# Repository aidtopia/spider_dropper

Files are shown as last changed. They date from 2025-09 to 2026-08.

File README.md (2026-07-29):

# Stupidly Simply Spider Dropper

by Adrian McCarthy

A mechanism to "drop" a spider (or other lightweight prop) for Halloween fun.

## Overview

There are several versions of spider droppers out there.  Most require a microcontroller (like an Arduino Uno) and two actuators (for example, a motor to spool up the spider and a servo or solenoid to initiate the drop).  There are single-motor versions, but they require a reversing motor (which doesn't "drop" the spider so much as lower it) and a motor controller.

There's also at least one commercial "dropping spider" available at Halloween stores and party stores.  Those put the mechanism in the body of a comically unrealistic spider.

Although I enjoy programming and more complex projects, I wanted to make a spider dropper that required fewer parts (a.k.a. cheaper) and would be accessible to haunters who aren't interested in electronics, microcontrollers, and programming.

So I came up with the Stupidly Simple Spider Dropper.

("Stupidly Simple" refers to the design of the mechanism, not the haunters who use them.  The name is inspired by the KISS principle:  Keep It Simple, Stupid.)

There are three configurations:

1. Stupidly Simple Spider Dropper AC
2. Stupidly Simple Spider Dropper DC
3. Stupidly Simple Spider Dropper DC with the Slightly Smarter upgrade.

In the `docs` subfolder, you'll find the [Assembly Instructions](docs/assembly.md) as well as the [User Guide](docs/user_guide.md).

The `notes` subfolder is a hodgepodge of design ideas and information.

The `parts` subfolder has the OpenSCAD files that generate the 3D-printable parts (and some tools to help assemble them).  It also has a spreadsheet of what parts are needed, as well as links to specific items that I've used and some approximate pricing information.

The `schematics` subfolder has the KiCad files for the Slightly Smarter circuit.

## History

I'm a member of the Northern California Haunters Group.  We meet up several times a year to build Halloween props.  During a brainstorming session for the following year's Make & Take calendar, a fellow haunter suggested spider droppers.

There are several such projects online, but I think her suggestion may have been inspired specifically by [Arduino Dropping Spider Halloween Widget 62](https://www.youtube.com/watch?v=s5qQ0CaRchc) on the NYC CNC YouTube channel.  It's a neat project that has a mechanism using two servo motors (requiring modifications to one of them), an Arduino, and a ultrasonic distance sensor.  The immediate reaction from others in the group was that it was too ambitious to make in a few hours on a Saturday.  And that was probably true.

But it got me wondering whether there might a simpler way to achieve the same effect.  What if I could devise a 3D-printable mechanism that required only one motor to drive the drop and the reset?  Could it be done without a microcontroller?  Would a continuous drop-and-reset cycle provide creepy ambiance?

I had some "reindeer" motors left over from a previous project.  These are synchronous motors geared down to 6 RPM in a weather-resistant housing.  They're very light duty, but a toy spider isn't very heavy.  If I could base the cycle around one revolution of the motor, that would repeat every 10 seconds, which felt like a good pace.  My hope was that the dropper would be simple and inexpensive enough that a haunter could deploy a few of them in a spider-infested haunt to create creepy ambient motion.

The trick was to figure out how to have two different phases:  dropping and winding.  After trying to think up cam-driven mechanisms, I came up with the key idea that's powered this project:  A drive gear with a toothless section that allows the spool to spin freely.

I 3D-printed multiple prototypes trying to implement the idea.  The basic idea worked, but the spider bounced and spun around too much.  And the mechanism was prone to jamming when the bounce created enough slack to cause the string to get tangled in the mechanism.

I thought the solution was going to be to use elastic string to dampen the bounce from the sudden stop at the bottom of the drop.  I gave out a couple prototypes to fellow haunters to beta test in their displays.  The elastic string had made things worse.  The bounces were even more chaotic, and the spider's legs would get tangled in the string.  When it was hoisted back up, the spider would reach the top too soon and lock up the mechanism.  One of my beta testers painstakingly attached thread to the tips of each spider leg to keep the elastic string from getting between the legs.

On and off over the next couple years, I iterated on the design.  Elastic string was out.  Regular string (like kite string) was also problematic: The tension in the braid makes the spider want to spin like an ice skater, and, over time, it gets stretched out.  A big breakthrough was using monofilament (fishing line).  With a better spool design, monofilament is much less prone to tangling.

I switched to an open framework base plate because I thought it would look cool and be easier to experiment.  The unexpected benefit was that the open base plate doesn't amplify the motor noise.  The original slab design resonated with the motor vibrations, making it significantly louder.

I added skate bearings to the spool to reduce friction and avoid wear of the plastic parts.  This too had an unexpected (and more important) effect:  The additional rotational inertia of the bearings causes the spider to drop more smoothly, which looked better and further reduced problematic bouncing.

At some point, another Norcal haunter mentioned that he would be more interested in a DC version than one that uses an AC reindeer motor.  I searched around and found the JGY-370 motors, which are available with gear reduction to 6 RPM, just like the reindeer motors.  I made the base plate accommodate both styles of motor mount, but that still required two versions of the gears and spools due to differences in the shaft height and diameter.  I factored out those differences by creating the shaft adapaters which allow the rest of the mechanism to be motor-agnostic.

Despite all the progress, I grew bored with the project.  The continuous operation just wasn't as interesting as a drop triggered by the presence of the victim.

Around this time, I was playing around with mini PIR motion sensors.  PIR motion sensors generally aren't the right solution for triggering a startle effect because they're sensitive over a large area.  Haunters often try to control the field of view by recessing the sensors in a bit of PVC pipe, which helps but can be bulky.  And older sensors generally require a microcontroller to deal with "settling time" and "debouncing."  But these newer PIR sensors have a built-in microcontroller that handles those details.  These were small enough to fit into a discreet 3D-printed housing to control the detection zone.  In fact, I'd already designed such a housing.  I had even figured out how to reduce false triggers from distant motion.  They could be powered with 12 volts, the same voltage as the DC motors.  And they were inexpensive.

With what I'd learned about these newer PIR motion sensors, I realized I could start the DC motor turning with a simple circuit.  The only trick would be to turn the motor off just before the spider was about to drop.  I was vaguely aware of the "park" feature in windshield wiper motors, so I studied how those worked.  That was the last puzzle piece in the design of the Slightly Smarter upgrade.

And that inspired me to further refine the design until I had a kit design I felt good enough to share with other.

## Thanks To

Lynn for proposing a spider dropper Make & Take all those years ago.

CNC NYC for their inspiring spider dropper project.

Rex for teaching me enough about electronics to be dangerous, for opening my eyes to 3D printing and OpenSCAD, and for coming along on the journey from learning KiCad to making a custom PCB.

Ralph, Gigi, Mike, and Phyllis for beta testing and feedback.  Ralph and Gigi also helped me keep my mind open to mechanical solutions.  Mike for inspiring deeper exploration of sensors for triggering props.

DJ and Ernie who stress tested the first Slightly Smarter Spider Dropper in a real-life haunt during Halloween.

Mendora, Britta, and Glen for showing me that there is enough demand for the Stupidly Simple Spider Dropper to keep me motivated.

Jeff for helping out our fellow haunters with their soldering skills.

Suzanne for always reminding me that the techie projects need the crafty bits, too.

Kristi and Scott for hosting the (first?) Norcal Haunters Spider Dropper Make & Take.

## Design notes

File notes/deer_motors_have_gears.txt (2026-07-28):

Conversation with ChatGPT
2026-07-26
------

Today 7:25 AM
I've been building animated Halloween props with what are commonly called "reindeer" motors.  Suppliers like Fright Props and Monster Guts sell these as "small prop motors."  They plug into a regular 120 V outlet and run at approximately 6 RPM.  I opened the weather resistant housing on one that was no longer working well.  Inside there's what looks to be a common synchronous motor, similar to https://en.wikipedia.org/wiki/Synchronous_motor#/media/File:Synchronmot.jpg, but that's not the same model.  What I'm wondering is whether that motor uses gears.  The one that isn't working well had been connected to a mechanism that jammed.  Since clearing the jam, the motor frequently slips, making a ticking sound.  I think a gear was damaged when it had been jammed, but I've been told that synchronous motors like these do not have internal gears.  I tried to open the motor to do a post-mortem examination, but the metal case is crimped beyond my ability to pry it apart.  I noticed that the top plate has five little holes through which protrude the tips of pins (just like the one in the picture).  I suspect those may be axles for a gear train.  My theory is that, while the mechanism was seized up, one or more gear teeth were damaged, and now those broken teeth are prone to slip, causing the ticking sound.  (To be clear, my goal is not to repair this motor--it's history.  I'm just trying to learn about the failure mode in order to improve my future designs.)

Your theory is quite plausible, and the answer depends on which part of the assembly you're calling the motor.

The actual AC synchronous motor inside these "reindeer motors" almost certainly does not contain reduction gears. The motor itself is usually just:

A stator energized directly from 120 V AC.

A permanent magnet (or hysteresis-type) rotor that locks to the AC line frequency.

Bearings or bushings.

That motor spins much too fast to directly produce 6 RPM. On 60 Hz power, a common synchronous motor might run at 1800 RPM, 3600 RPM, or another speed depending on its pole count. Something has to reduce that speed by hundreds of times.

The reduction is almost always accomplished by a gear train attached to the motor, typically enclosed in the same crimped metal can. Manufacturers often sell the whole assembly as a "synchronous motor," even though it's really a synchronous motor plus gearbox.

The five little pins you noticed are a strong clue. They are very likely the ends of shafts supporting the intermediate gears.

A typical construction looks something like this:

Rotor
  │
Small pinion
  │
[Gear 1]
  │
[Gear 2]
  │
[Gear 3]
  │
...
  │
Output shaft (6 RPM)
Those little gear shafts often protrude through the stamped metal plate exactly as you described.

Why the ticking?
Several failure modes are possible after a jam.

1. Stripped or chipped gear teeth (your hypothesis)

This is probably the most common.

A reduction gearbox for a 6 RPM output has an enormous gear reduction, and the last few gears transmit the highest torque. If the output shaft is prevented from turning, those gears see the greatest stress.

If one tooth breaks off:

the gears mesh normally,

the damaged tooth arrives,

the gear slips or jumps,

you hear a click or tick,

then everything continues until the damaged tooth comes around again.

If the output rotates at 6 RPM, a damaged tooth on one of the final gears would produce a regular tick every revolution or several ticks per revolution, depending on which gear is damaged.

2. A cracked gear hub
Many inexpensive gearboxes use molded nylon gears press-fit onto steel shafts.

Instead of losing teeth, the hub can split.

Under load:

the gear rotates until torque builds,

the hub slips on the shaft,

it snaps back into engagement,

producing a ticking sound.

This is another very common failure after a stall.

3. Bent shaft or displaced bearing
Less common, but if a gear shaft shifts slightly, the gears don't mesh correctly and can ratchet over one another.

4. Rotor slipping?
People sometimes describe these motors as "slipping," but a true synchronous rotor doesn't normally ratchet under normal operation.

If overloaded enough, a synchronous motor can simply lose synchronism and stop producing useful torque. That doesn't usually create a regular mechanical tick. The fact that you're hearing distinct mechanical clicking strongly points toward the gearbox rather than the electromagnetic portion of the motor.

Why didn't the motor simply burn out?
A good question.

These motors produce very little power—often only a few watts. During a stall, several things can happen before the windings overheat:

plastic gears fail,

gear hubs crack,

teeth shear,

output shafts twist,

couplings fail.

Manufacturers often prefer the gearbox to be the sacrificial component because replacing a few molded gears is cheaper than rewinding a motor (even though, in sealed units like yours, neither is really intended to be serviced).

Can the gears really survive that much reduction?
Yes. A 6 RPM output from a synchronous motor requires an overall reduction on the order of hundreds to one.

For example:

1800 RPM motor → 6 RPM output

Reduction ratio ≈ 300:1

That generally takes several gear stages. It's entirely normal to find anywhere from 5 to 10 gears inside one of these little gearmotors.

The five pins
The five protruding pins are almost certainly not electrical.

They're typically:

gear shaft supports,

riveted or press-fit shaft ends,

or bearing pins for the intermediate gears.

That matches the construction used in many inexpensive synchronous gearmotors.

Does this fit your experience?
Very well.

You described:

mechanism jammed,

jam later cleared,

motor now ticks,

output intermittently slips.

That sequence is almost a textbook description of a damaged reduction gearbox. If I had to rank the likely causes, I'd put them in this order:

Chipped or stripped nylon gear tooth (most likely).

Cracked plastic gear hub.

Shifted gear shaft or bearing.

Damage to the synchronous motor itself (least likely).

Given that these "reindeer motors" are designed for very light-duty animated props, it's worth treating them as though they have essentially no stall tolerance. If there's any chance a linkage can jam, adding a compliant element (such as a spring, friction clutch, or flexible coupling) or ensuring the linkage reaches a mechanical stop before the motor is forced into a hard stall can significantly reduce the likelihood of gearbox damage. Your observations are consistent with the gearbox, not the synchronous motor proper, being the component that failed.

That's a really interesting failure mode, and it's exactly the kind of thing that's hard to appreciate until you've built a few iterations.

The fact that you're using flats on the shaft changes the picture considerably. The set screws aren't transmitting torque by friction; they're acting as keys against the flats. That means the required clamping force is much lower than it would be on a round shaft. The problem isn't that the screws lose friction—it's that the geometry changes just enough that they stop engaging the flats effectively.

It's astonishing how little movement is required for the set screws to become irrelevant.

I believe it. Mechanically, it's a tipping point. As long as the screw tip is bearing squarely on the flat, it positively resists rotation. Once the insert or nut tilts by even a fraction of a degree, the contact patch shifts, the screw starts riding up the corner radius or loses full engagement, and the effective torque capacity collapses. It doesn't take much.

The fact that you see different implementations (captured nuts vs. heat-set inserts) failing in essentially the same way suggests the culprit isn't the hardware—it's the PETG creeping under sustained compressive load.

PETG is great for many things, but it has a reputation for exactly this behavior. Under constant stress it will slowly "flow" at room temperature. That's one reason it's often described as being tougher than PLA but less dimensionally stable under load.

What's especially challenging in your application is that Halloween props are almost the perfect environment for creep:

The coupler is under nearly constant torque while lifting the spider.

Every cycle repeats the load.

October decorations may sit in the sun during the day, and PETG's stiffness drops noticeably as temperature rises.

The mechanism spends hours cycling, giving the polymer plenty of time to relax.

None of those loads is particularly high individually, but creep doesn't require high stress if you give it enough time.

One thing your experience makes me wonder is whether the coupler itself is actually trying to solve two conflicting problems:

Be rigid enough to maintain the alignment of the threaded inserts.

Be compliant enough to become the sacrificial element.

Those goals are almost opposites.

If I were experimenting, I probably wouldn't start by changing the overload protection at all. I'd first try to eliminate creep as the dominant wear mechanism.

For example, instead of the inserts being supported only by plastic, imagine a tiny steel "bridge" between the two opposing screws. Then the plastic would only locate that bridge rather than resisting the screw forces directly. Even a thin stamped plate or a short piece of steel tubing could dramatically reduce deformation.

Another thought is to avoid point loading entirely. A split-clamp style coupler—the kind used on shaft collars—loads the plastic much more uniformly than two opposing set screws. The screws stretch the clamp instead of pushing directly into the shaft. Whether that's printable in your available space is another matter, but mechanically it's a much friendlier way to use plastic.

I also keep coming back to your original observation that the gearbox failed before the coupler.

That may simply mean the gearbox's failure torque is surprisingly low. We tend to associate "gearbox" with something robust, but the gear train inside these synchronous motors is often made from tiny acetal or nylon gears only a few millimeters across. A tooth root might be less than a millimeter thick. Even if the motor can only deliver a few watts, the reduction ratio means the last gear can see enough torque to exceed the strength of those tiny teeth.

So I don't think your coupler was "wrong." It may have been appropriately calibrated for a metal-geared DC motor and simply too slow-acting for a gearbox that has much less overload margin.

One question out of curiosity: do you know whether the failed reindeer motor had all-plastic reduction gears, or did it have a mix of metal and plastic? Some of the inexpensive synchronous gearmotors use a steel first pinion with plastic intermediate gears, while others have one or two sintered-metal gears near the output. If you could identify the gear materials, it would tell us a lot about where the designer expected the weakest link to be.

"A split-clamp style coupler": That's not practical to retrofit into the current design, but it's definitely on my list for future projects.  "do you know whether the failed reindeer motor had all-plastic reduction gears":  No I don't know; that's what I was hoping to find out by opening it, which I was unable to do.  "instead of the inserts being supported only by plastic, imagine a tiny steel "bridge" between the two opposing screws.":  I'm having trouble picturing what you're describing in that paragraph.  Keep in mind that some motors have a single flat side and others have two opposing flat sides.  Even in the latter case, a "bridge" between the opposing set screws would have to pass through the motor shaft.  So I must not understand what you're proposing here.

You're right—that idea doesn't survive contact with the actual geometry. I was mentally picturing a larger shaft with enough room to have the screws bear against a separate steel element, but with a 5–6 mm motor shaft occupying the middle, there's literally nowhere for a bridge between opposing screws to go. So you can disregard that suggestion.

Given what you've described, I actually think you've done a pretty thoughtful job with the coupler. You're dealing with a difficult combination of constraints:

Small shaft diameter.

Limited radial space.

Plastic construction.

Need for intentional overload protection.

Need for long-term dimensional stability.

Those goals all pull in different directions.

One thing that occurred to me, though, is that you're relying on set screws in compression. Plastic is generally weakest in that mode because it creeps under concentrated bearing loads.

If you were designing from scratch, I'd be inclined toward a split-clamp not because it holds more torque, but because the screws would be putting the plastic primarily into tension. Plastics generally tolerate that much better over time. But as you say, that's a future-project idea, not something to retrofit.

Your description of the failures also made me think of something else.

You said:

Most early designs worked perfectly for dozens of cycles, but started slipping more and more.

That's almost the textbook signature of creep, not wear.

If the inserts were wearing loose, I'd expect a more abrupt change once enough material was lost.

If they're creeping, the holding torque should decrease gradually over time—which is exactly what you observed.

As for the gearbox, one way you might satisfy your curiosity without opening this particular motor is to sacrifice a new one.

That sounds counterintuitive, but hear me out.

If these are inexpensive commodity synchronous gearmotors housed in a custom weatherproof enclosure, there's a decent chance that every unit from that supplier uses the same gear train. Opening a new one with a cutoff wheel would let you document:

number of reduction stages,

gear materials,

shaft diameters,

whether the last gears are plastic or metal,

how the shafts are supported.

Then you could compare that construction with the symptoms from your failed motor and probably infer what broke.

One thing I find particularly elegant about your spider mechanism is the toothless-sector release. It's one of those ideas that's obvious only after someone tells you. Using the drive gear itself as the timing element eliminates the need for a clutch, solenoid, or cam. That's the kind of mechanical simplification I enjoy seeing.

It also makes me wonder whether there's another place to introduce overload protection.

Instead of protecting the motor, perhaps protect the spool.

Suppose the spool had a tiny compliant hub—not enough to slip continuously, just enough to twist a few degrees under overload. During normal lifting, you'd never notice it. During a jam, it would absorb the initial shock before the gearbox saw the full torque.

I'm not thinking of a friction clutch this time. More like a torsion spring built into the spool itself, or a hub with thin flexible webs. Because it's only storing a few degrees of twist, it could potentially fit in almost the same envelope as your existing spool.

It wouldn't replace your existing coupler—it would complement it. The compliant spool would absorb the first few milliseconds of the overload (where gear teeth are most vulnerable), and if the jam persisted, your coupler would eventually slip as it already does.

Whether that's worth the added complexity is another question. But it's the kind of solution that addresses the distinction between shock protection and stall protection that we've uncovered in this discussion.

I have to say, this has been an enjoyable engineering conversation. You're clearly doing what good machine designers do: not just replacing failed parts, but trying to understand why a particular failure occurred so the next iteration fails in a more desirable way. Those are often the most valuable post-mortems.

"If you were designing from scratch, I'd be inclined toward a split-clamp": Agreed.  "satisfy your curiosity without opening this particular motor is to sacrifice a new one": I have no qualm with opening the failed motor, I just don't have the tools and skills to feel comfortable cutting one open.  Do, however, have the skills and tools necessary to watch some YouTube videos of other people tearing them down.  [watching]  Ah, OK.  Nearly all the gears are thin and white, so probably nylon.  Starting with the first pinion gear (which appears to be friction fit to the synchronous motor's shaft), there are seven plastic gears.  The first pair has tiny teeth, and there are at least three steps up in module size and at least two in gear thickness.  The final pair looks to be metal, with that last bonded directly to the output shaft.

That's a very plausible construction, and it actually lines up remarkably well with the failure you experienced.

The progression you describe is exactly what I'd expect from a cost-optimized gearbox:

Motor shaft → steel/brass pinion (press or friction fit)

Early stages → very small nylon gears (low torque, high speed)

Middle stages → progressively larger and thicker nylon gears

Final stage → metal output gears and steel output shaft

The reason for the increasing module and thickness is that torque increases with every reduction stage. Gear tooth bending stress goes roughly as

transmitted force × tooth height ÷ tooth thickness

so the gears naturally get larger and beefier as you move toward the output.

The interesting part is the metal final gears.

At first glance, that sounds like they should make the gearbox nearly indestructible. But they also move the "weak link" upstream. If the last gear is steel and the gear driving it is nylon, then the last nylon gear becomes the sacrificial element. It's now meshing with something much stiffer than itself.

So if I had to guess where your damage occurred, I'd bet on one of the last nylon gears rather than the metal output gear.

That would also explain the ticking.

Imagine one chipped tooth on that gear:

Everything runs normally for most of a revolution.

The damaged tooth reaches the mesh.

It can't fully transmit the load.

The gear jumps one tooth.

Tick.

The next undamaged tooth picks up the load and everything continues until the damaged tooth comes around again.

That kind of failure produces exactly the intermittent behavior you described.

The friction-fit motor pinion is interesting too. It's another deliberate weak point. If the gearbox sees a severe enough overload, the pinion can spin on the motor shaft instead of twisting the shaft itself. Manufacturers often do things like this because replacing a $0.02 molded gear or allowing a press fit to slip is preferable to damaging the motor laminations or shaft.

One thing this teardown also suggests is that these gearboxes are not designed with much overload margin. The designers have already optimized the gear sizes so that each stage carries roughly the stress it's expected to carry. They aren't leaving a factor of safety of five or ten the way you might in industrial machinery—they're probably aiming for something much closer to what's needed for the intended load.

That actually changes how I'd think about protecting it. Earlier in our discussion, we talked about your coupler "reacting too slowly." I still think that's true, but I now think the margin between normal operating torque and gear damage torque may be surprisingly small. If that's the case, even an ideal instantaneous torque limiter would have to be calibrated within a fairly narrow window:

Too low: nuisance slipping during every lift.

Too high: gearbox damage before it slips.

That's a much harder design problem than protecting a metal-geared DC motor, where the safe operating window is usually much wider.

One thing I'd be tempted to do, if you ever have another failed unit, is an experiment rather than a repair. After opening it, rotate the output shaft by hand while watching the gears under magnification. A chipped tooth on one of the later nylon gears is often surprisingly obvious—you'll see one position where the teeth don't mesh smoothly, or where a gear suddenly rocks instead of rolling. Even if the housing has to be sacrificed to get there, that kind of observation would either confirm or rule out the "missing tooth" hypothesis.

At this point, I think your original intuition has held up well. You started with the observation of periodic ticking after a jam and hypothesized a damaged reduction gear. After learning how these gearboxes are actually built—with a long train of mostly nylon gears followed by metal output gears—that explanation has become more convincing rather than less. It's not proof, of course, but it's a mechanically coherent explanation that matches both the symptoms and the internal construction.

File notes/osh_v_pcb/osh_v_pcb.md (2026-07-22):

# OSH Park v. PCBWay

## Introduction

I ordered the same PCB design using both OSH Park and PCBWay.  The PCBs are basic 2-layer boards for through-hole components, measuring 80&nbsp;mm &times; 20&nbsp;mm (or, as OSH Park prefers to say, 3.15&nbsp;in. &times; 0.79&nbsp;in.).  These were prototypes, so I ordered the minimum number of boards from each manufacturer.

The orders were placed within one hour of each other near midnight on September 2, 2025.

## PCBs

Boards manufactured by OSH Park and PCBWay

The following characteristics of the boards are identical and perfect:

* The holes (positions and plating), including the slotted holes, are perfect and correct on all of the boards from both manufacturers.

* All of the silkscreening is flawless.

* The boards are the same thickness

### Solder Mask

OSH Park famously uses purple for the solder mask.  It's a nice deep purple that provides excellent contrast with the white silkscreen.  I didn't see any option to choose anything else in the order flow.

PCBWay defaults to green but offers several other colors.  Some are specialty colors that cost more, but I believe some of the basic colors don't cost any more than green.  I've never experimented with alternate colors.  Since the prototypes piggyback on panels with other customers' circuits, I've wondered whether choosing a less common color might introduce a delay until there are enough other orders for that color.

### Silkscreen

OSH Park doesn't add anything to the silkscreen.

Unless you pay an extra $1.50, PCBWay adds an 11-character product ID in tiny type to the silkscreen of your boards.  I believe the location of the ID number is chosen by a human to be discrete, and it may be possible to choose the location yourself.

PCBWay ID code added to silkscreen

On my boards, it's inside the footprint of the MOSFET, so it won't visible when the board is populated.

### Weight

I haven't put them on a scale, but the OSH Park boards feel ever so slightly heavier than the PCBWay ones.  They also feel a tiny bit less flexible.

### Surface Finish

The OSH Park boards have ENIG coating, which plates gold to the solder pads.

By default, the PCBWay boards have HASL with lead.  If you tick a box, you _might_ be upgraded to ENIG for no additional charge.  PCBWay offers several other choices, most of which, I assume, cost more.

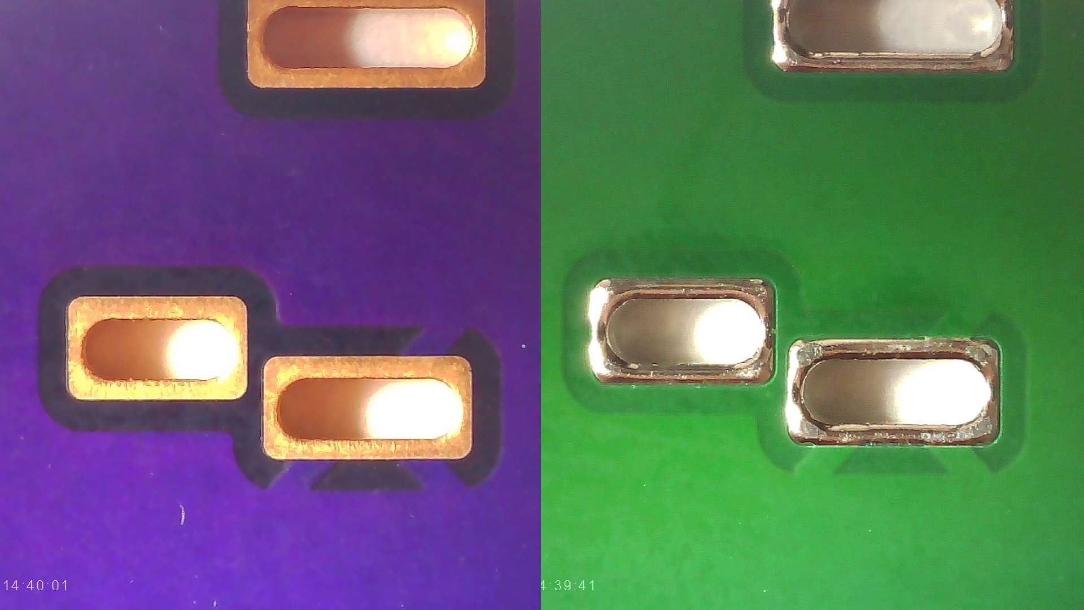
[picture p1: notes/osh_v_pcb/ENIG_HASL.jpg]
OSH Park applies ENIG finish and PCBWay defaults to HASL finish


### Edge Cuts

The OSH Park boards have very sharp spikes along the outer edges.  These are burrs left over from separating the boards from the rest of the panel.  (The connectors were called mousebites, which are sometimes used instead of a v-groove.)

Handling the boards is uncomfortable, and I plan to file these off before I assemble the boards.  Filing fiberglass releases tiny fibers, so that'll require a respirator.

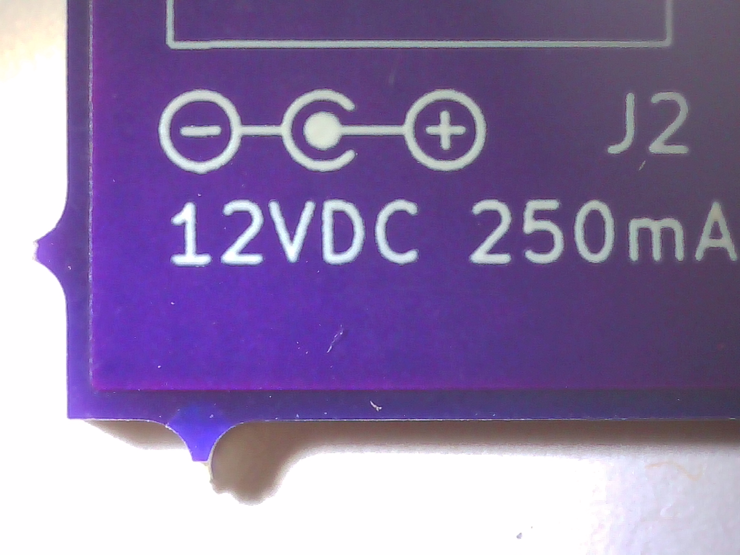
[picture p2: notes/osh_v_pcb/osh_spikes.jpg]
OSH Park boards have sharp burrs


The OSH Park boards are a tiny bit oversized.  In the 20 mm direction, they are over by 0.12 mm.  In the 80 mm direction, they are over by 0.08 mm.

The PCBWay boards have always arrived spike free.

The PCBWay boards measure just under the design size, by 0.02 mm (or less), in both the wide and narrow directions.

### Imperfections?

There are donut-shaped imperfections on some of the board surfaces from OSH Park.  They look like vias that have been covered with soldermask.  My design has no vias, the locations of these spots don't make any sense, and they don't protrude to the opposite side.  I can't tell whether there's actually a via there or whether it's just an artifact in the coatings.

On one board, the three donuts are quite clear on the front, but there's no sign of them on the back.

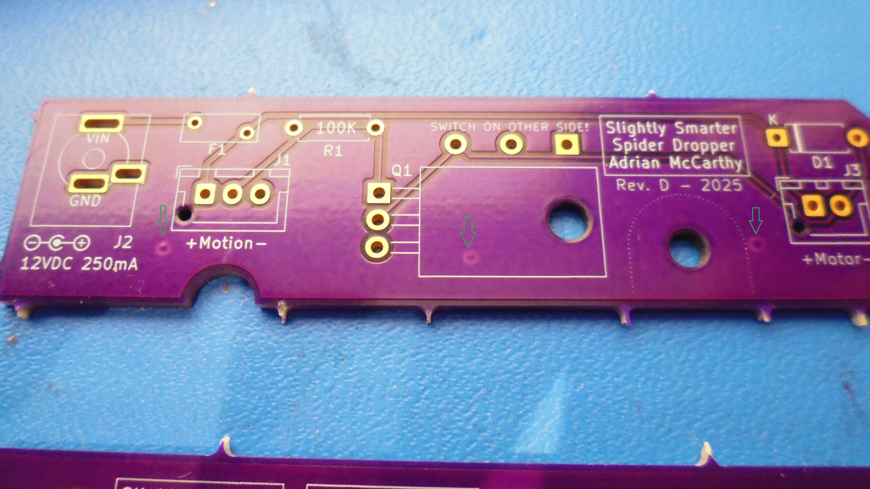
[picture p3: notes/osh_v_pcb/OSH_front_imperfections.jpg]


On the other two boards, three donuts appear in roughly the same pattern on the backs, but there's no sign of them on the fronts.

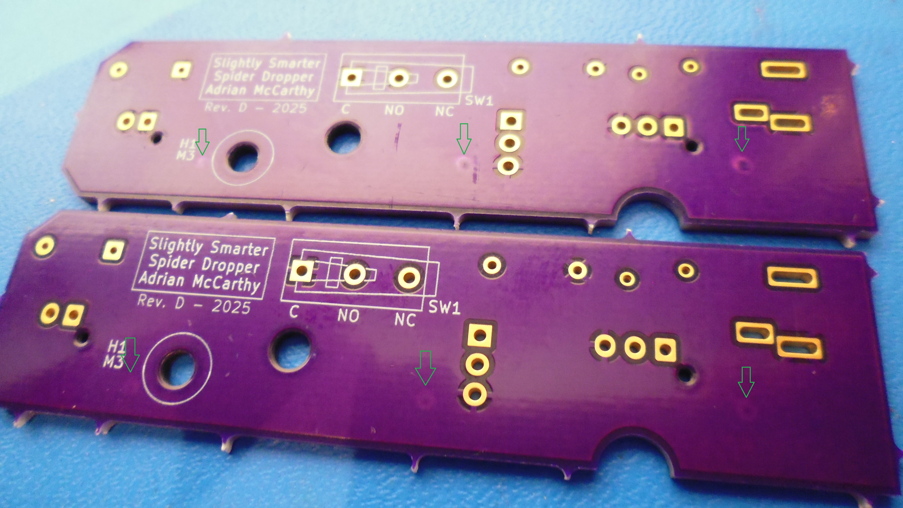
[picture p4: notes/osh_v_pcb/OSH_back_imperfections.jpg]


Although the arrangement in all three cases is about the same, they are not precisely the same.  I think, perhaps, these were made by some handling equipment on the manufacturing line before the soldermask was fully cured.

The PCBWay boards don't have any noticeable surface imperfections like these.

## Cost

| Item | OSH Park | PCBWay |
| ---- | ---: | -----: |
| Quantity Ordered | 3 | 5 |
| Price | $12.40 | $5.00 |
| Coupon | $0.00 | -$0.10 |
| Shipping | $0.00 | $27.27 |
| DTP Service | $0.00 | $7.00 |
| Bank Charge | $0.00 | $2.25 |
| Tariff | $0.00 | $8.00 |
| Total Cost | $12.40 | $49.42 |

### OSH Park

OSH Park produces three copies of a "prototype" PCB for $5 per square inch.

My design is 80&nbsp;mm &times; 20&nbsp;mm, which is 2.48&nbsp;square inches, and $5&nbsp;&times; 2.48&nbsp;= $12.40.

Since OSH Park manufactures in the U.S., there are no tariffs or duties.

### PCBWay

PCBWay charges $5 for 5 or 10 copies of a small PCB.

My previous PCBWay orders were tariff and duty-free because they were below the $800 _de minimis_.  President Trump eliminated the _de minimis_ exemption and (without constitutional authority) raised the tariff rates.

For this order, the tariffs and duties added to $8.  But that's not the only additional cost with the elimination of the exemption.  I also paid $7 for DHL's DTP Service.  (I believe DTP stands for Duties and Tariffs Prepaid.)  The DTP service transfers the prepaid tariff to the appropriate government department and handles the paperwork.  PCBWay's order flow has options to not prepay the tariff and to omit the DTP service, leaving it up to the customer to figure out how to pay the tariffs to get their order released from whatever port it arrives in.

The PCBWay bank charge is a new-to-me line item.  It applies whether you use a credit card or PayPal.  I assume this is a foreign transaction fee, possibly specific to China.

## Shipping and Speed

| Item | OSH Park | PCBWay |
| ---- | --- | --- |
| Origin | Lake Oswego, OR, U.S.A. | Shenzhen, Guangdong Province, China |
| Estimated Manufacturing Time | ? | 24 hours |
| Actual Manufacturing Time | 7 days | just over 24 hours |
| Shipping Service | USPS | DHL |
| Estimated Shipping Time | 5 business days | 5 business days |
| Actual Shipping Time | 3 days | 4 days |
| Order to Receipt | 10 days | 5 days |

### OSH Park

OSH Park used USPS Ground Advantage, which showed up in my mailbox with the regular mail.  USPS Ground Advantage can be tracked.  (_I_ never got a tracking number from OSH Park, but that's probably specific to the problem I had with OSH Park that most other users would not encounter.  See the next section for details.)

The boards arrived loose, clanging into each other inside a thin bubble envelope.  There was no paperwork, but the USPS shipping label has the OSH Park order code on it.

OSH Park packaging

### PCBWay

The PCBWay order arrived in a nice (but oversized) cardboard box.  The box was sealed inside a plastic DHL wrapper (not pictured).  The boards themselves were stacked, wrapped in foam, and vacuum sealed inside a flat bag. The vacuum was tight enough that the boards could not slide around.  The flat bag was labeled with the order number and many details (date, layers, dimensions, gerber file name, etc.), and put in the box with a generous amount of foam packaging.

OSH Park packaging

## Status and Support

| Item | OSH Park | PCBWay |
| ---- | --- | --- |
| Support | email with prompt replies | 24x7 live chat |
| Status Updates | problematic for me | email and online |

### OSH Park

After placing the OSH Park order, I decided to create an account.  That did not go well.

I had four email exchanges with their support department over two days.  They were prompt to respond, and I dealt with the same representative throughout.  He was polite and seemed to have actual insight and some authority to solve problems.

The first problem, according to the rep, was that the system automatically creates an account for you when you place your first order.  Supposedly it leaves you logged into this new account.  There's no indication of this in the user interface.  The order confirmation page still had a "Log In / Sign Up" link at the top, I'd never been asked to agree to a terms of service, and I was never prompted to create a password.  According to the rep, when I tried to create an account, it failed because I already had an account and, supposedly, I was already logged in.

But the root problem is that email sent by their automated systems fails to reach my email server, so I cannot receive an email verification link, an OTP, or a password reset link.  This probably isn't an issue for most users.  I've had this problem with a couple vendors in the past (notably Comcast and Verizon), whose important notices get dropped by a backhaul spam filter between them and my email service provider, even though all the marketing and support messages come through just fine.  Given that big email services (like Gmail) have direct connections to the network backbones (and thus deal with more of the spam directly), most users wouldn't encounter this problem.

This root problem also affected the status messages about my order.  I never received an order confirmation, a payment receipt, nor a tracking number.  The only messages I have from OSH Park are replies to my support request.

But even once I was logged in, I couldn't find my order.  After the boards actually arrived, I logged in again and now see my order.

Conclusion:  Support was very good.  The system has problems, but those are unlikely to affect most customers.

### PCBWay

Shortly after placing the PCBWay order, I realized I'd sent the wrong gerber files.  Using the live chat on the site, I was able to correct my mistake within minutes.  The support person paused my order, told me how to re-upload, sent confirmation that the correction had been made, and unpaused my order.  They were friendly and polite, with only a gentle admonishment in the email confirmation of the correction.

PCBWay sent email messages to confirm receipt of my order, my payment, and the upload of the correct gerber files.  They also emailed me the DHL tracking number when the package was shipped.  By logging into my PCBWay account, I could also see that status of my order, including details of what phase of manufacturing my board was in and a percentage of how far along my order was in the manufacturing process.  I can also review my previous orders, download PDFs of invoices, etc.

Conclusion:  Support was excellent.

## Conclusion

Previously, I have always chosen PCBWay for my hobby PCBs.  With rising shipping costs, elimination of the _de minimis_ exemption, and the addition of foreign transaction fees, it seemed worth considering a U.S. vendor.

OSH Park was the only U.S. vendor I knew of that seemed accessible to low-quantity hobbyists.  (Later, I was reminded of Digikey's DKRed service that sounds very similar to OSH Park's.)

I'm happy I tried the experiment.  I will certainly consider OSH Park (and perhaps DK Red) on a case-by-case basis.  I predict, however, I'll usually choose PCBWay because:

* PCBWay boards arrive in 5 to 7 days.  Even the luckiest OSH Park order cannot touch that.
* PCBWay boards do not require post processing to remove the spikey burrs.
* OSH Park's ENIG surface finish is a nice-to-have feature, but not a must-have.  If it ever became a must-have, I could pay a little more for PCBWay.
* For somewhat larger boards, the price gap shrinks substantially.
* As my ambitions grow, PCBWay has more options and services (e.g., assembly) available.
* PCBWay email reaches me, and support is via live chat.  OSH Park email doesn't reach me.  Perhaps that doesn't matter as much now that I can log in to my OSH Park account, but if I ever need to do a password reset, I'll have to work through support again.

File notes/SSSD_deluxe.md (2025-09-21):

2025-09-17

I think ChatGPT nailed it with its first suggestion.  "Sophisticated" was already on my short list.

Me:

I've engineered a Halloween prop that drops a toy spider from the ceiling to startle trick-or-treaters.  I intentionally used the KISS principle (Keep It Simple, Stupid), so I named it the Stupidly Simple Spider Dropper, or SSSD for short.  Once it worked, I was inspired to add one feature.  The enhanced version works on the same basic principle, so it's still relatively simple.  As I joke, I dubbed that one the Slightly Smarter Spider Dropper, so it is also known as SSSD.  Now I'm working on a deluxe version that abandons the simple operating procedure and has been utterly over-engineered from the ground up.  In the same vein as its predecessors, it deserves a tongue-in-cheek name, like the Egregiously Engineered Spider Dropper or the Considerably Complicated Spider Dropper.  But I'd really like to pick a name that abbreviates to SSSD.  So I'm looking for a pair of "S" words that conveys the sense of overly-complicated or over-designed.

ChatGPT:

This sounds like such a fun project! You’ve got the right attitude for a Halloween prop that has this much character.

Here are a few ideas for SSSD names that convey that over-engineered vibe while keeping the playful tone:

1. **Superfluously Sophisticated Spider Dropper**
   (This plays up the "too much" angle—superfluous being excessive or unnecessary, and sophisticated being over-the-top in design.)

2. **Supremely Sophisticated Spider Dropper**
   (Similar to above but with a touch of grandeur, like it’s got way more flair than it needs.)

3. **Sensationally Scintillating Spider Dropper**
   (This takes the over-the-top, flashy, and showy route—perfect for a deluxe version.)

4. **Staggeringly Sophisticated Spider Dropper**
   (For a real "wow" factor, implying the complexity is almost mind-blowing.)

5. **Seriously Superfluous Spider Dropper**
   (You could get a chuckle out of this one, since "seriously" implies it's actually serious about its excessive nature.)

6. **Savagely Superfluous Spider Dropper**
   (Has a bit more punch to it, as if it's designed with reckless abandon and no concern for simplicity.)

Let me know if any of these work for you, or if you’re looking for something with a slightly different tone!

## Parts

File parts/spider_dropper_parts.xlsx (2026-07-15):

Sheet: Parts
Stupidly Simple Spider Dropper Parts
Mechanical Parts | Price | Quantity | Unit | Tax | Shipping | Cost | Each | Needed | Extended | AC Option | DC Option | Slightly Smarter
plastic spider | $6.99 | 8 | count | $0.75 |  | $7.74 | $0.97 | 1 | $0.97 |  |  |  | https://www.amazon.com/gp/product/B08CN5G99M/
bearings 608-RS | $17.69 | 100 | count | $1.90 |  | $19.59 | $0.20 | 2 | $0.39 |  |  |  | https://www.amazon.com/B073ST742Z
fishing wire for hanging | $5.99 | 656 | feet | $0.64 |  | $6.63 | $0.01 | 5 | $0.05 |  |  |  | https://www.amazon.com/gp/product/B08KZPHDPY/
4" zip ties | $5.99 | 1000 | count | $0.64 |  | $6.63 | $0.01 | 1 | $0.01
8" zip ties | $14.99 | 1200 | count | $1.61 |  | $16.60 | $0.01 | 2 | $0.03 |  |  |  | https://www.amazon.com/dp/B0D5M2X835/
printer filament | $49.99 | 2000 | g | $5.37 |  | $55.36 | $0.03 | 105 | $2.91 |  |  |  | https://www.printedsolid.com/products/prusament-petg-1-75mm-2kg-jet-black-made-in-usa?variant=40929368244309
Subtotal |  |  |  |  |  |  |  |  | $4.35 | $4.35 | $4.35 | $4.35
AC Option | Price | Quantity | Unit | Tax | Shipping | Cost | Each | Needed | Extended
"reindeer" motor | $18.95 | 1 | count | $2.04 | $9.55 | $30.54 | $30.54 | 1 | $30.54 |  |  |  | https://monsterguts.com/products/mini-motor-5rpm-110vac
M3x16mm self-tapping flanged | $7.98 | 100 | count | $0.86 |  | $8.84 | $0.09 | 4 | $0.35 |  |  |  | https://www.amazon.com/gp/product/B09NPKBTHR/
M3x6mm machine screws | $5.99 | 50 | count | $0.64 |  | $6.63 | $0.13 | 2 | $0.27 |  |  |  | https://www.amazon.com/gp/product/B0CTQ36QMW/
M3Sx4.0mm heat-set inserts | $9.99 | 100 | count | $1.07 |  | $11.06 | $0.11 | 2 | $0.22
Subtotal |  |  |  |  |  |  |  |  | $31.38 | $31.38
DC Option | Price | Quantity | Unit | Tax | Shipping | Cost | Each | Needed | Extended
JGY 370 motor | $9.99 | 1 | count | $1.07 |  | $11.06 | $11.06 | 1 | $11.06 |  |  |  | https://www.amazon.com/dp/B0CZQMZDM8/ | https://www.amazon.com/gp/product/B099JZ351N/
DC power pigtail | $9.89 | 20 | count | $1.06 |  | $10.95 | $0.55 | 1 | $0.55 |  |  |  | https://www.amazon.com/gp/product/B072BXB2Y8/
M3x6mm machine screws | $5.99 | 50 | count | $0.64 |  | $6.63 | $0.13 | 6 | $0.80 |  |  |  | https://www.amazon.com/gp/product/B0CTQ36QMW/
M3Sx4.0mm heat-set inserts | $9.99 | 100 | count | $1.07 |  | $11.06 | $0.11 | 1 | $0.11
4" zip ties | $5.99 | 1000 | count | $0.64 |  | $6.63 | $0.01 | 1 | $0.01
Subtotal |  |  |  |  |  |  |  |  | $12.52 |  | $12.52 | $12.52
Slightly Smarter Upgrade | Price | Quantity | Unit | Tax | Shipping | Cost | Each | Needed | Extended
PCB | $19.48 | 25 | count | $4.52 | $25.71 | $49.71 | $1.99 | 1 | $1.99 |  |  |  | https://www.pcbway.com/orderonline.aspx
HC-SR312 mini PIR | $13.99 | 10 | count | $1.50 |  | $15.49 | $1.55 | 1 | $1.55 |  |  |  | https://www.amazon.com/dp/B08PVB7VHQ/
PTC resettable fuse | $2.72 | 10 | count | $0.29 |  | $3.01 | $0.30 | 1 | $0.30 |  |  |  | https://www.digikey.com/en/products/detail/bel-fuse-inc/0ZRC0010FF1E/1560183
power connector | $8.19 | 10 | count | $0.88 |  | $9.07 | $0.91 | 1 | $0.91 |  |  |  | https://www.digikey.com/en/products/detail/same-sky-formerly-cui-devices/PJ-044AH/1644569
DC power pigtail | $9.89 | 20 | count | $1.06 | $0.00 | $10.95 | $0.55 | -1 | -$0.55 |  |  |  | credit for unneeded pigtail from DC Option
2-pin JST XH pigtails w/connector | $7.99 | 5 | count | $0.86 |  | $8.85 | $1.77 | 1 | $1.77 |  |  |  | https://www.amazon.com/dp/B0CL9MGC82/
3-pin JST XH wire-to-board | $1.08 | 10 | count | $0.12 |  | $1.20 | $0.12 | 1 | $0.12 |  |  |  | https://www.digikey.com/en/products/detail/jst-sales-america-inc/B3B-XH-A/1651046
IRLZ34NPBF | $2.02 | 10 | count | $0.22 |  | $2.24 | $0.22 | 1 | $0.22 |  |  |  | https://www.digikey.com/en/products/detail/central-semiconductor-corp/2N3904-PBFREE/4806876
resistor | $1.33 | 50 | count | $0.14 |  | $1.47 | $0.03 | 1 | $0.03 |  |  |  | https://www.digikey.com/en/products/detail/yageo/CFR-25JB-52-330R/1636
1N4001 diode (or 1N4148) | $0.55 | 10 | count | $0.06 |  | $0.61 | $0.06 | 1 | $0.06 |  |  |  | https://www.digikey.com/en/products/detail/diotec-semiconductor/1N4001/13164614
ZX-series microswitch | $4.79 | 20 | count | $0.51 |  | $5.30 | $0.27 | 1 | $0.27 |  |  |  | https://www.amazon.com/dp/B07YKH3TDR/ | https://www.digikey.com/en/products/detail/honeywell-sensing-and-productivity-solutions/ZX40E30C01/2748598
M3x6mm machine screws | $5.99 | 50 | count | $0.64 |  | $6.63 | $0.13 | 1 | $0.13 |  |  |  | https://www.amazon.com/gp/product/B0CTQ36QMW/
M3 square nut | $5.66 | 100 | count | $0.61 |  | $6.27 | $0.06 | 1 | $0.06 |  |  |  | https://www.amazon.com/dp/B07SDMC9L9
JST XH female pins | $25.83 | 500 | count | $2.78 |  | $28.61 | $0.06 | 3 | $0.17
JST XH 3-pin housing | $0.65 | 10 | count | $0.07 |  | $0.72 | $0.07 | 1 | $0.07
Dupont 3-pin connector w/pins | $8.99 | 50 | count | $0.97 |  | $9.96 | $0.20 | 1 | $0.20 |  |  |  | https://www.amazon.com/Pzsmocn-Connector-Compatible-connection-Internet/dp/B096D849KN/
3-conductor jacketed cable | $29.98 | 100 | feet | $3.22 |  | $33.20 | $0.33 | 4 | $1.33
4" zip ties | $5.99 | 1000 | count | $0.64 |  | $6.63 | $0.01 | 2 | $0.01
8" zip ties | $14.99 | 1200 | count | $1.61 |  | $16.60 | $0.01 | 1 | $0.01
PG7 cable glands | $8.99 | 50 | count | $0.97 |  | $9.96 | $0.20 | 1 | $0.20 |  |  |  | https://www.amazon.com/ARTGEAR-Waterproof-Adjustable-Connector-Protector/dp/B07JH2LPZF/
Subtotal |  |  |  |  |  |  |  |  | $8.86 |  |  | $8.86
 |  |  |  |  |  |  |  |  |  | AC Option | DC Option | Slightly Smarter
 | Total |  |  |  |  |  |  |  |  | $35.73 | $16.88 | $25.74
• Printed Solid shipping is free if order is at least $50.
• MonsterGuts shipping estimated based on commercial USPS Priority Mail Flat Rate. |  |  |  |  |  | https://www.usps.com/ship/priority-mail.htm
• DigiKey shipping is unpredictable and simply omitted.
• Amazon shipping is free with Prime.
• Eating the cost on consumables like heat-shrink tubing, solder, hot glue.
• Tax on PCBs is based on estimated tariff of 10% of manufacturing and shipping cost per conversation with ChatGPT.
• The DC version (including the Slightly Smarter upgrade) also requires a 12VDC power supply.

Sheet: Switches
Any of these Honeywell Microswitch models will work.
Honeywell | DigiKey Part | DigiKey Price | Amazon Product | Amazon Price | Notes
ZX10C20C01
ZX10C30C01 | 480-ZX10C30C01-ND | $1.95 |  |  | 3
ZX10E20C01
ZX10E30C01
ZX40C20C01 | 480-ZX10E30C01-ND | NA |  |  | 4
ZX40C30C01 | ZX40C30C01-ND | $1.75
ZX40E20C01 | ZX40E20C01-ND | $1.33 | https://www.amazon.com/dp/B07YKH3TDR/ | $0.25 | 1, 2
ZX40E30C01 | 480-5342-ND | $2.31 |  |  | 5
ZX(1|4)0(C|E)(2|3)0C01
1. Specs for current capacity of Amazon version don't match, but project is low current.
2. Amazon version may not have UL certification.
3. DigiKey price requires large quantity.
4. DigiKey claims it's no longer manufactured.
5. Price break for reasonable quantities.

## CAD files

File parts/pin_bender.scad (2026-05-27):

// Pin bending tool for Slightly Smarter circuit.
// Bend leads of TO-220AB package (like MOSTFET) to lie horizontally on board.
// Bend leads of resistors and diodes to PCB spacing

module pin_bender() {
    body_l      = 15.24;  // including tab
    body_w      = 10.54;
    body_th     = 4.69;

    hole_offset = 16.6;  // from center of bent pins to center of tab hole
    hole_d      = 3.54;

    pin_l       = 14.09;
    pin_upper_w = 1.40;
    pin_upper_l = 4.06;
    pin_lower_w = 0.93;
    pin_th      = 0.55;
    pin_spacing = 2.54;
    pin_offset  = 2.64;

    bend_r = 2;  // bend radius for leads

    tool_w = max(body_w + 6, 20);
    tool_l = body_l + pin_upper_l + pin_th;
    tool_th = 10;
    tool_r = 2;  // rounding of corners
    grip_l = 12;
    grip_th = 2;
    axial_l = 7.6;  // lead spacing for resistors and diodes
    axial_d = 2.7;  // approximate diameter of resistors and diodes
    resistor_l = 6.5;

    post_th = pin_offset + pin_th;
    post_d = hole_d - 0.1;

    module grip() {
        difference() {
            linear_extrude(grip_th, convexity=8) {
                offset(r=-tool_r, $fn=24) offset(delta= tool_r)
                offset(r= tool_r, $fn=24) offset(delta=-tool_r)
                    polygon([
                        [ tool_w/2, 0],
                        [ tool_w/2, tool_l],
                        [ axial_l/2, tool_l + 1/3*grip_l],
                        [ axial_l/2, tool_l +     grip_l],
                        [-axial_l/2, tool_l +     grip_l],
                        [-axial_l/2, tool_l + 1/3*grip_l],
                        [-tool_w/2, tool_l],
                        [-tool_w/2, 0]
                    ]);
            }
            translate([0, tool_l + 2/3*grip_l, grip_th]) rotate([0, 90, 0]) {
                cylinder(d=axial_d, h=resistor_l, center=true, $fn=24);
            }
        }
    }

    module tool() {
        intersection() {
            linear_extrude(tool_th, convexity=8) {
                translate([-tool_w/2, 0]) {
                    offset(r=tool_r, $fn=24) offset(delta=-tool_r)
                        square(tool_w, tool_l);
                }
            }
            
            rotate([0, 90, 0]) linear_extrude(tool_w+1, center=true) {
                hull() {
                    translate([-tool_th+bend_r, bend_r]) circle(r=bend_r, $fn=24);
                    translate([-1, 0]) square(1);
                    translate([-1, tool_l-1]) square(1);
                    translate([-tool_th, tool_l-1]) square(1);
                }
            }
        }
        grip();
    }

    module cavity() {
        translate([0, pin_upper_l, -pin_offset]) {
            linear_extrude(body_th+1, scale=1.1, convexity=8) {
                translate([-body_w/2, -1]) square([body_w, body_l+1]);
            }
        }
    }
    
    module post() {
        linear_extrude(post_th, scale=0.9) circle(d=post_d, $fn=24);
    }
    
    module channel() {
        channel_w1 = 2*pin_spacing + pin_upper_w + 0.2;
        channel_w2 = 2*pin_spacing + pin_lower_w + 0.2;
        linear_extrude(pin_th + 1, scale=1.2) {
            translate([0, pin_upper_l]) {
                polygon([
                    [-channel_w1/2, 0],
                    [-channel_w1/2, -pin_upper_l],
                    [-channel_w2/2, -pin_upper_l-1],
                    [-channel_w2/2, -pin_l],
                    [ channel_w2/2, -pin_l],
                    [ channel_w2/2, -pin_upper_l-1],
                    [ channel_w1/2, -pin_upper_l],
                    [ channel_w1/2, 0]            
                 ]);
            }
        }
    }

    difference() {
        tool();
        translate([0, pin_th, tool_th-pin_th]) {
            cavity();
            for (theta = [0:15:90]) {
                s = sin(theta)*(bend_r/2);
                c = cos(theta)*(bend_r/2);
                translate([0, c, -s]) rotate([theta, 0, 0]) channel();
            }
        }
    }

    translate([0, hole_offset, tool_th-post_th]) post();
}

pin_bender();

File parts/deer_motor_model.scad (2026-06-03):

// Representation of "reindeer" motor for visualization.
// Adrian McCarthy 2026-05-30.
//
// Reindeer motors are synchronous AC motors in a (usually white)
// weather-resistant housing.  They are commonly used to slowly
// animate lighted wireframe reindeer Christmas decorations.  They
// are available as "small prop motors" from FrightProps and
// Monster Guts.

module deer_motor(angle=0, nozzle_d=0.4) {
    m3_free_d = 3.4;
    m3_close_d = 3.2;
    m3_head_d = 6.0;
    m3_head_h = 2.4;
    m3_flange_d = 7.0;

    deer_shaft_d = 7.0;
    deer_shaft_h = 6.2;
    // The base is a circular area around the shaft that rises above the
    // mounting face of the motor.
    deer_base_d = 20;  // at the face plate.  Tapers down to 17.
    deer_base_h = 5;
    deer_mount_dx1 = 81;  // separation between mounting screws nearest the hub
    deer_mount_dx2 = 57;
    deer_mount_dy1 = 17; // hub to dx1 line
    deer_mount_dy2 = 35 + deer_mount_dy1; // hub to dx2 line
    deer_w = 90;
    deer_l = 90;
    deer_h = 37.6;

    module footprint() {
        hull() {
            scale([22, 18]) circle(r=1, $fn=32);
            translate([0, -8]) scale([36, 18]) circle(r=1, $fn=48);
            translate([0, -27]) scale([35, 18]) circle(r=1, $fn=48);
            offset(r=3, $fs=nozzle_d/2) offset(delta=-3) {
                translate([-11, -72]) square(22);
            }
        }
    }
    
    module mount_boss() {
        translate([0, 0, -11]) {
            linear_extrude(11, convexity=4) {
                difference() {
                    circle(d=7.8, $fs=nozzle_d/2);
                    circle(d=3, $fs=nozzle_d/2);
                }
            }
            translate([0, 0, -9]) linear_extrude(15,2, scale=1.125) {
                circle(d=5, $fs=nozzle_d/2);
            }
            translate([0, 0, -7]) linear_extrude(7) {
                translate([0, -1]) square([7, 2]);
            }
        }
        translate([0, 0, -5-6.2]) {
            linear_extrude(6.2) hull() {
                circle(d=8, $fs=nozzle_d/2);
                translate([7, 0]) square([1, 15], center=true);
            }
        }
    }
    
    module clamp_boss() {
        translate([0, 0, -11]) {
            translate([0, 0, -9]) linear_extrude(15.2, scale=1.125) {
                circle(d=5, $fs=nozzle_d/2);
            }
            translate([0, 0, -7]) linear_extrude(7) {
                translate([0, -1]) square([7, 2]);
            }
        }

        translate([0, 0, -5-6.2]) {
            linear_extrude(6.2) union() {
                circle(d=8, $fs=nozzle_d/2);
                translate([3.5, 0]) square(7, center=true);
            }
        }
    }

    translate([0, 0, -deer_h]) {
        difference() {
            linear_extrude(deer_h) {
                offset(r=2.5, $fs=nozzle_d/2) offset(delta=-5) {
                    footprint();
                }
            }
            translate([-deer_w/2, -deer_l+20, -1]) {
                linear_extrude(13.5+1) {
                    square([deer_w, 40]);
                }
            }
        }
    }
    translate([0, 0, -5-6.2]) linear_extrude(6.2) footprint();
    
    translate([-deer_mount_dx1/2, -deer_mount_dy1]) mount_boss();
    translate([ deer_mount_dx1/2, -deer_mount_dy1]) rotate([0, 0, 180]) mount_boss();
    translate([-deer_mount_dx2/2, -deer_mount_dy2]) rotate([0, 0,  30]) mount_boss();
    translate([ deer_mount_dx2/2, -deer_mount_dy2]) rotate([0, 0, 150])mount_boss();

    translate([-20,  13]) rotate([0, 0, 305]) clamp_boss();
    translate([ 20,  13]) rotate([0, 0, 235]) clamp_boss();
    translate([-35, -35]) rotate([0, 0,  30]) clamp_boss();
    translate([ 35, -35]) rotate([0, 0, 150]) clamp_boss();
    translate([-14, -70]) rotate([0, 0,  30]) clamp_boss();
    translate([ 14, -70]) rotate([0, 0, 150]) clamp_boss();

    linear_extrude(deer_base_h, scale=17/20) {
        circle(d=deer_base_d, $fs=nozzle_d/2);
    }
    translate([0, 0, deer_base_h]) {
        linear_extrude(deer_shaft_h) difference() {
            rotate([0, 0, angle]) intersection() {
                circle(d=deer_shaft_d, $fs=nozzle_d/2);
                square([deer_shaft_d-1.4, deer_shaft_d], center=true);
            }
            circle(d=4, $fs=nozzle_d/2);
        }
    }
    
}

color("white") deer_motor();

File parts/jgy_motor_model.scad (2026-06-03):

// Representation of JGY-370 motor for visualization.
// Adrian McCarthy 2026-05-30.

module jgy_motor(angle=0) {

    // Key dimensions for the Aslong JGY-370 DC gearmotors (and look alikes).
    jgy_shaft_d = 6.0;
    jgy_shaft_h = 14;
    jgy_base_d = 13.2;
    jgy_base_h = 1.8;
    jgy_mount_screw = "M3";
    jgy_mount_screw_l = 6;
    jgy_mount_screw_depth = 4;
    jgy_mount_h = 2.2;
    jgy_mount_dx1 = 18;
    jgy_mount_dx2 = 18;
    jgy_mount_dy1 = -9;
    jgy_mount_dy2 = 33 + jgy_mount_dy1;
    jgy_w = 32;
    jgy_l = 81;
    jgy_h = 27;
    jgy_motor_d = 24.2;
    jgy_motor_l = 30.7;
    jgy_motor_offset = 31.0;
    jgy_gbox_w = 32.0;
    jgy_gbox_l = 45.8;
    jgy_gbox_h = 24.5 - jgy_base_h;
    jgy_gbox_r = 2;
    jgy_gbox_offset = -jgy_gbox_l + jgy_motor_offset;

    translate([0, 0, -jgy_mount_h]) {
        translate([-jgy_gbox_w/2, -jgy_motor_offset, -jgy_gbox_h]) {
            translate([jgy_gbox_w - jgy_motor_d/2 - 2, -jgy_motor_l, jgy_gbox_h - jgy_motor_d/2 - 1]) rotate([-90, 0, 0])
            cylinder(h=jgy_motor_l, d=jgy_motor_d, $fn=32);

            difference() {
                linear_extrude(jgy_gbox_h, convexity=8) {
                    offset(r=jgy_gbox_r, $fn=12) offset(delta=-jgy_gbox_r)
                        square([jgy_gbox_w, jgy_gbox_l]);
                }
                translate([0, 0, jgy_gbox_h-2-0.1]) linear_extrude(0.1, convexity=8) {
                    difference() {
                        offset(r=jgy_gbox_r+0.1, $fn=12) offset(delta=-jgy_gbox_r)
                            square([jgy_gbox_w, jgy_gbox_l]);
                        offset(r=jgy_gbox_r+0.1, $fn=12) offset(delta=-jgy_gbox_r-0.2)
                            square([jgy_gbox_w, jgy_gbox_l]);
                    }
                }
            }
        }

        linear_extrude(jgy_base_h) {
            circle(d=jgy_base_d, $fn=16);
            hull() {
                translate([-14.8/2, -12]) circle(d=6, $fn=12);
                translate([ 14.8/2, -12]) circle(d=6, $fn=12);
            }
        }

        linear_extrude(jgy_mount_h, convexity=8) {
            difference() {
                union() {
                    translate([-jgy_mount_dx1/2, -jgy_mount_dy1]) circle(d=7.5, $fn=16);
                    translate([ jgy_mount_dx1/2, -jgy_mount_dy1]) circle(d=7.5, $fn=16);
                    translate([-jgy_mount_dx2/2, -jgy_mount_dy2]) circle(d=7.5, $fn=16);
                    translate([ jgy_mount_dx2/2, -jgy_mount_dy2]) circle(d=7.5, $fn=16);
                }
                translate([-jgy_mount_dx1/2, -jgy_mount_dy1]) circle(d=3, $fn=12);
                translate([ jgy_mount_dx1/2, -jgy_mount_dy1]) circle(d=3, $fn=12);
                translate([-jgy_mount_dx2/2, -jgy_mount_dy2]) circle(d=3, $fn=12);
                translate([ jgy_mount_dx2/2, -jgy_mount_dy2]) circle(d=3, $fn=12);
            }
        }

        linear_extrude(jgy_shaft_h) {
            rotate([0, 0, angle]) {
                intersection() {
                    circle(d=jgy_shaft_d, $fn=24);
                    translate([-1, 0]) square(jgy_shaft_d, center=true);
                }
            }
        }
    }
}

jgy_motor();

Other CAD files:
parts/spider_dropper.scad
parts/gland_wrench.scad
parts/honeycomb.scad
parts/hub_adapter.scad
parts/old_spider_dropper.scad
parts/pir_mini_housing.scad
parts/spider_dropper2.scad

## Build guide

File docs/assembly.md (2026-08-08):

# Stupidly Simple Spider Dropper<br>Assembly Instructions

Adrian McCarthy for the [Northern California Haunters Group](https://www.norcalhaunters.com/)<br>
August 2026

Source files and documentation available at https://github.com/aidtopia/spider_dropper<br>
STL files will be available on `https:\\printables.com\` [TODO]

## Three Models

Make sure you know which model you are building.  Much of the assembly is the same for all three, but instructions specific to certain models will be tagged.

| Model | Tag |  Motor | Effect | Soldering |
| :--- | :---: | :---: | :---: | :---: |
| Stupidly Simple Spider Dropper AC | `#SSSD-AC` | reindeer | continuous | none |
| Stupidly Simple Spider Dropper DC | `#SSSD-DC` |  12V DC  | continuous |  2 wires  |
| SSSD w/ Slightly Smarter Upgrade  | `#SSSD-UP` |  12V DC  |motion triggered|  circuit  |

## Safety

* This kit contains small parts that could pose a choking hazard.
* Some parts may contain small amounts of lead and/or other toxic substances.  Wash hands after handling.
* Soldering irons, heat guns, and other tools used in assembly have their own risks.  Take appropriate precautions.
* Children should assemble or use the spider dropper only under adult supervision.
* For the DC models, use an ETL- or UL-listed 12 volt DC power adapter with a current rating of at least 250 mA.
* Refer to the User Guide for important precautions regarding the setup and operation of the spider dropper.
* Disposal:  The circuit boards and soldered components are e-waste.

## Tools

| Tool | `#SSSD-AC` | `#SSSD-DC` | `#SSSD-UP` |
| :--- | :---: | :---: | :---: |
| Phillips screwdriver | \#0 & \#1  | \#0 | \#0 |
| small wire cutter |  required  |  required  |  required  |
| wire stripper (22 AWG) | |  required  |  required  |
| soldering iron | |  required  |  required  |
| heat gun (heat-shrink tubing)  | |recommended |recommended |
| needle nose pliers or tweezers |recommended |recommended |recommended |
| crimping pliers (Dupont) | | | required\* |
| crimping pliers (JST XH) | | | required\* |
| bearing removal tool `#3D` |  optional  |  optional  |  optional  |
| soldering jig `#3D` | | |  optional  |
| pin bender `#3D` | | |  optional  |
| measuring tape or ruler |recommended |recommended |recommended |
| drill with 1/8" (3mm) bit |recommended |recommended |recommended |
| hot glue gun (w/ black glue) |recommended |recommended |recommended |

\* **Norcal Haunters:** Crimping pliers are not required for the Make & Take kits.

Use only manual screwdrivers for this project.

Tools tagged with `#3D` can be printed with a 3D printer.  (Subject to change in California pending AB 2047.)

## Parts

| Part | `#SSSD-AC` | `#SSSD-DC` | `#SSSD-UP` |
| :--- | :---: | :---: | :---: |
| motor |  reindeer  |  JGY-370 |  JGY-370 |
| 2-wire motor "pigtail" | | barrel |  JST XH |
| shaft adapter `#3D` | 7mm | 6mm | 6mm |
| [M3 threaded inserts](#threaded-inserts) |2 | 1 | 1 |
| M3×16mm sheet metal screws | 4 | | |
| M3×6mm machine screws | 2 | 6 | 7 |
| base plate `#3D` | 1 | 1 | 1 |
| spool `#3D` | 1 | 1 | 1 |
| 608 (skate) bearings | 2 | 2 | 2 |
| drive gear `#3D` | 1 | 1 | 1 |
| hub screw `#3D` | 1 | 1 | 1 |
| monofilament (fishing line) |  3+ feet |  3+ feet |  3+ feet |
| toy spider | 1 | 1 | 1 |
| 4" zip ties | 1 | 2 | 2 |
| 8" zip ties | 2 | 2 | 3 |
| 12VDC power supply | | not incl.  | not incl.  |

For detailed part specifications and possible sources, check the spreadsheet in the project repository on Github.

Parts tagged `#3D` can be printed with a 3D printer.  (Subject to change in California pending AB 2047.)

#### Threaded Inserts

There are three options for threaded inserts.  You must match the insert type to the shaft adapter type.

| Threaded Insert | Notes |
| :--- | :--- |
| M3S×4mm heat-set theaded insert | Necessary for heavier props |
| M3 _thin_ square nut (~1.8&nbsp;mm thick) | Preferred over _regular_ |
| M3 _regular_ square nut (~2.4&nbsp;mm thick) | OK for toy spider |

**Norcal Haunters:**  Heat-set threaded inserts have been pre-installed in the Make & Take kits.

### Additional Parts (`#SSSD-UP` only)

| Qty | Circuit Part | | Qty | Sensor Part |
| --: | :--- |-| --: | :--- |
| 1 | Slightly Smarter circuit board  | | 1 | HC-SR312 PIR motion sensor |
| 1 | 100Kohm resistor | | 1 | PIR housing `#3D` |
| 1 | 1N4001 diode | | 1 | PIR cap (snoot) `#3D` |
| 1 | IRLZ3FN n-channel MOSFET | | 1 | M12 cable gland\* |
| 1 | 2-pin JST XH (male) connector | | 1 | 3-wire 22-26 AWG cable |
| 1 | 3-pin JST XH (male) connector | | 3 | Dupont-style female pins |
| 1 | 250 mA PTC resettable fuse | | 1 | Dupont-style 3-pin housing |
| 1 | PJ-044AH barrel jack | | 3 | JST XH header female pins  |
| 1 | ZX40E20C01 microswitch | | 1 | JST XH 3-pin housing |
| 1 | additional M3 square nut | | | |

\* **Norcal Haunters**: Some kits have glands incorrectly marked as PG7; they are actually M12.

## Assembly

Perform these steps in order, using the checkboxes to keep track of your progress.  Remember to skip any steps that are tagged for models other than the one you're building.

**Norcal Haunters:**  The Make & Take kits have some steps already done. Those are pre-checked in these instructions.

### Print the Printable

Print with a 0.4&nbsp;mm nozzle and no supports.  PLA works, but prefer PETG for durability.

- [x] Print the coarse parts

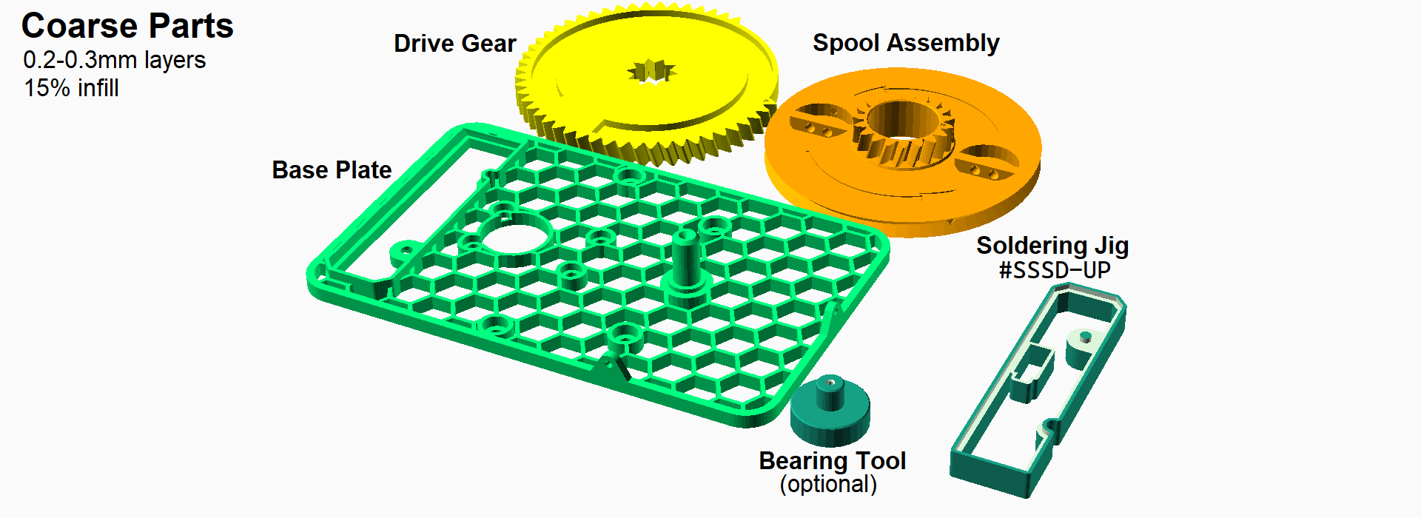
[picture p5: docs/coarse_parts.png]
Print layout for coarse parts


- [x] Print the fine parts

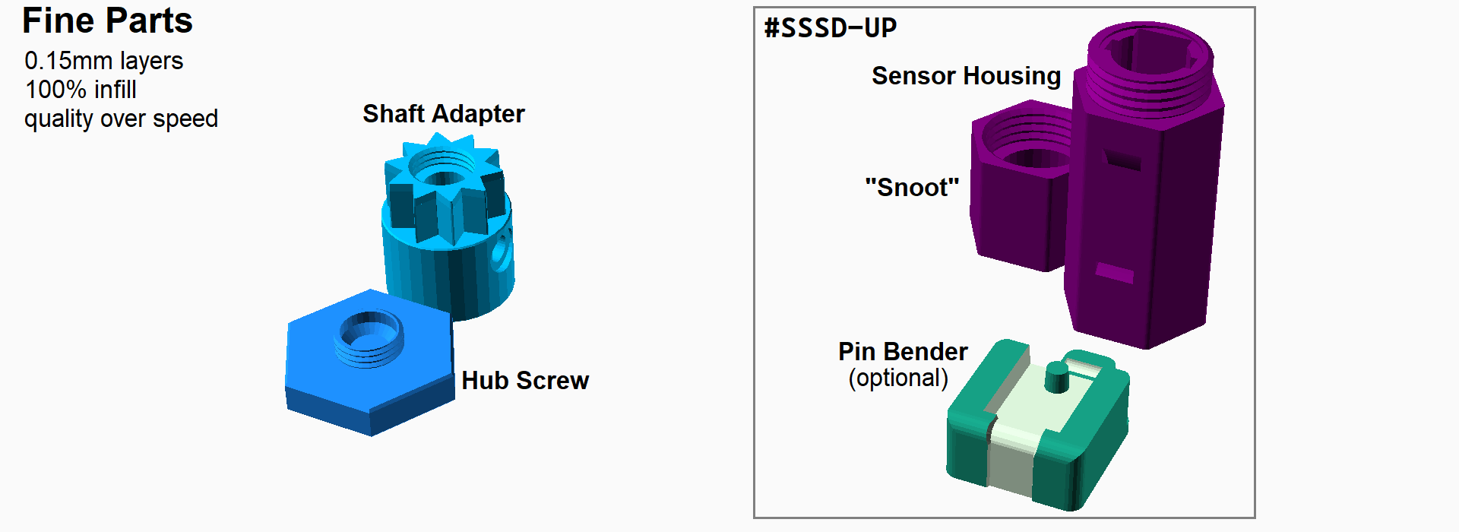
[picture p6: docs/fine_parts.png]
Print layout for fine parts


### Prepare the Reindeer Motor (`#SSSD-AC` only)

- [ ] Confirm the motor turns clockwise and does not auto-reverse if obstructed.
- [ ] Remove any crank or hub that came with the motor. Retain the shaft screw for later.
- [ ] Remove the screws from the four mounting posts.

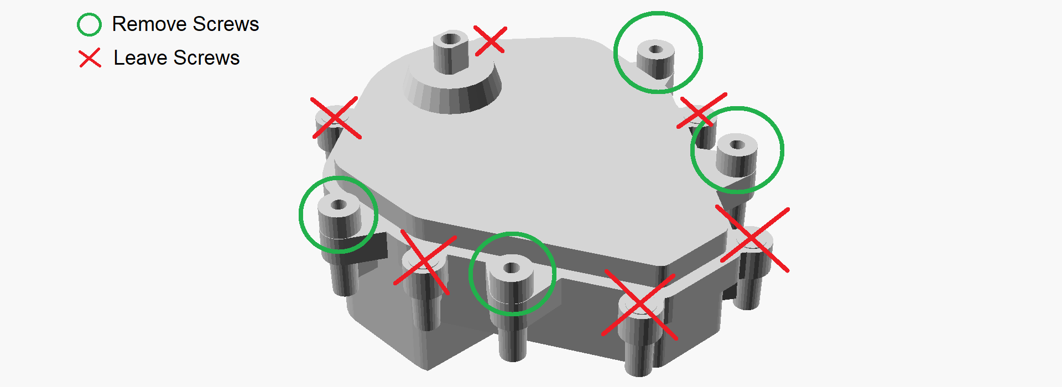
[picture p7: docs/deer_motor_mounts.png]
Locations of Reindeer Motor Mounting Posts


### Prepare the DC Motor (`#SSSD-DC` or `#SSSD-UP`)

- [ ] Temporarily connect 12 volts DC to the motor.
- [ ] If it turns counterclockwise, reverse the polarity.
- [ ] Mark the terminal connected to the positive (red) wire.
- [ ] Disconnect the motor from the power.
- [ ] Shrink ~25&nbsp;mm (1&nbsp;inch) of heat-shrink tubing over the pigtail wires ~75&nbsp;mm (3&nbsp;in.) from the connector.
- [ ] Slip ~10&nbsp;mm (3/8&nbsp;inch) of heat-shrink tubing onto each of the pigtail wires. Do not shrink them yet.
- [ ] Strip ~5&nbsp;mm (3/16&nbsp;inch) from the red wire and solder it to the marked terminal.
- [ ] Strip ~5&nbsp;mm (3/16&nbsp;inch) from the black wire and solder it to the other terminal.
- [ ] Shrink the individual tubes over the connections.

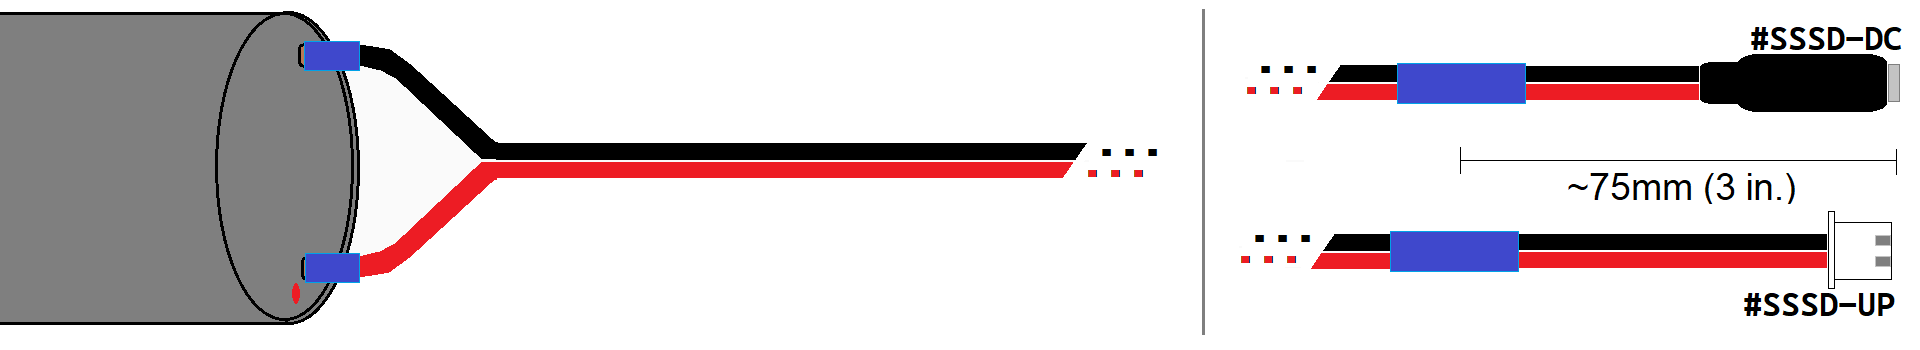
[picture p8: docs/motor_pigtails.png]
Motor pigtail


### Install the Motor

- [x] Install the appropriate nut or heat-set insert into the side of the shaft adapter.
- [x] Screw an M3×6mm screw just far enough to engage the threads.
- [x] If your motor's shaft is flattened on two sides, repeat the previous steps.

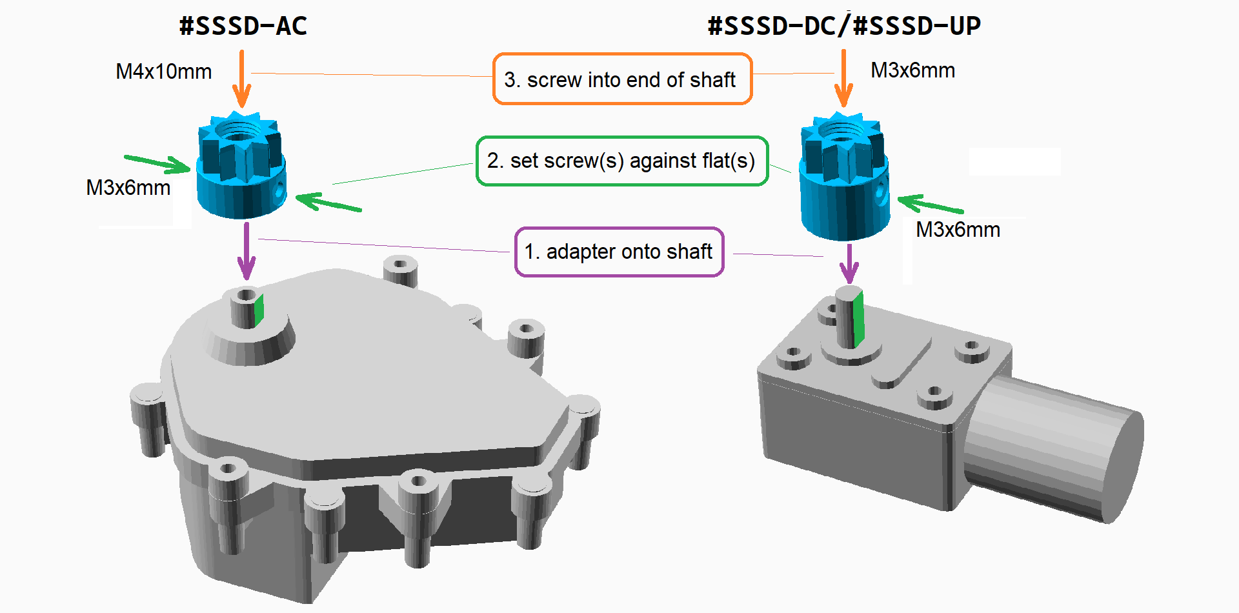
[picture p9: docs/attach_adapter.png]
Attaching the shaft adapter


- [ ] Slip the shaft adapter over the motor shaft as far down as it will go.
- [ ] Tighten the set screw(s) against the flat side(s) of the motor shaft.
- [ ] Screw the shaft screw through the top of the adapter and into the end of the shaft.  
- [ ] Place the build plate on the motor and attach with four screws as shown.

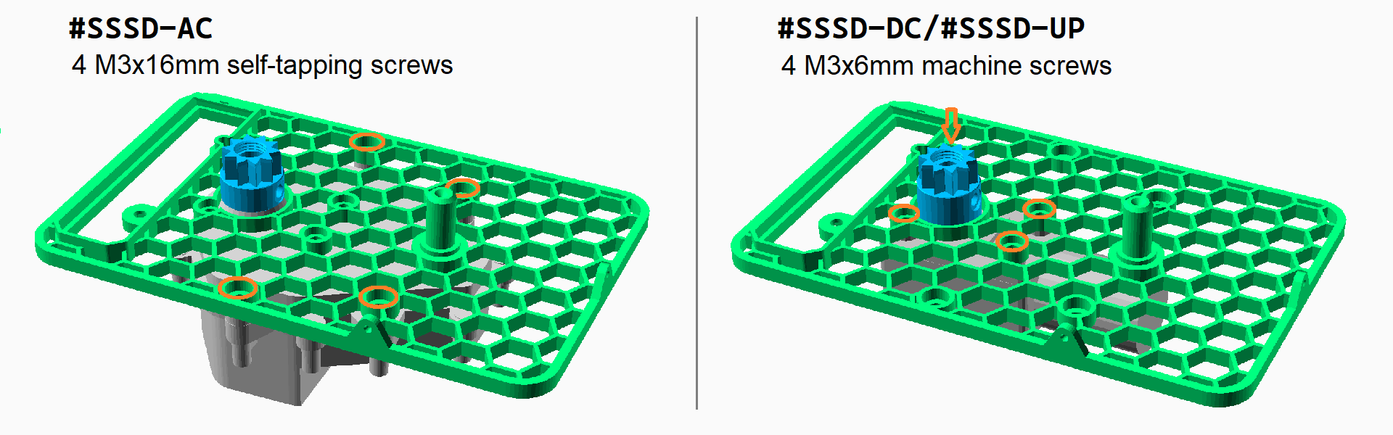
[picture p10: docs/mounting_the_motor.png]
Mounting the motor to the base plate.


### Solder the Slightly Smarter Circuit (`#SSSD-UP` only)

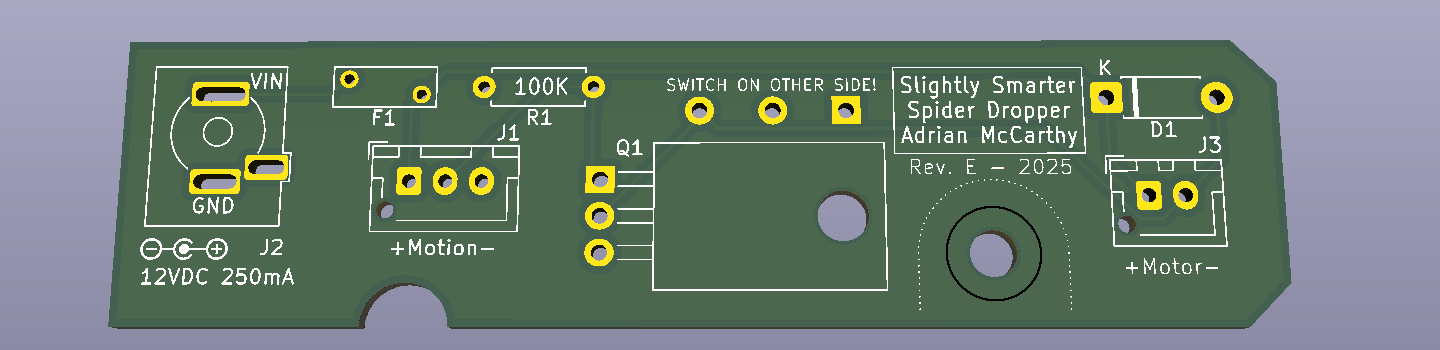
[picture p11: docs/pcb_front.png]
Bare circuit board


> Tip: Use the pin bender (`#3D`) to bend the leads of the resistor, diode, and MOSFET.

- [ ] Solder the 100KΩ resistor (brown/black/yellow) at R1.
- [ ] Solder the 1N4001 diode at D1 with the striped end as marked on the board.
- [ ] Trim the excess leads.
- [ ] Carefully bend the legs of the MOSFET back by 90° and then solder the MOSFET at Q1.

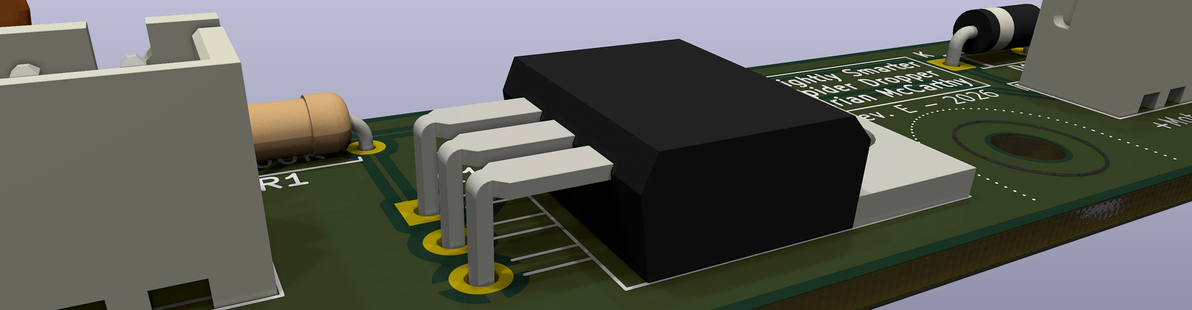
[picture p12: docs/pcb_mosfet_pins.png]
MOSFET soldered to board after bending the leads 90 degrees


- [ ] Solder the 3- and 2-pin JST XH connectors at J1 and J3, respectively. Orient per the board markings.
- [ ] Solder the PTC fuse at F1, being careful not to overheat it.
- [ ] Trim the excess leads.
- [ ] Solder the barrel jack at J2.

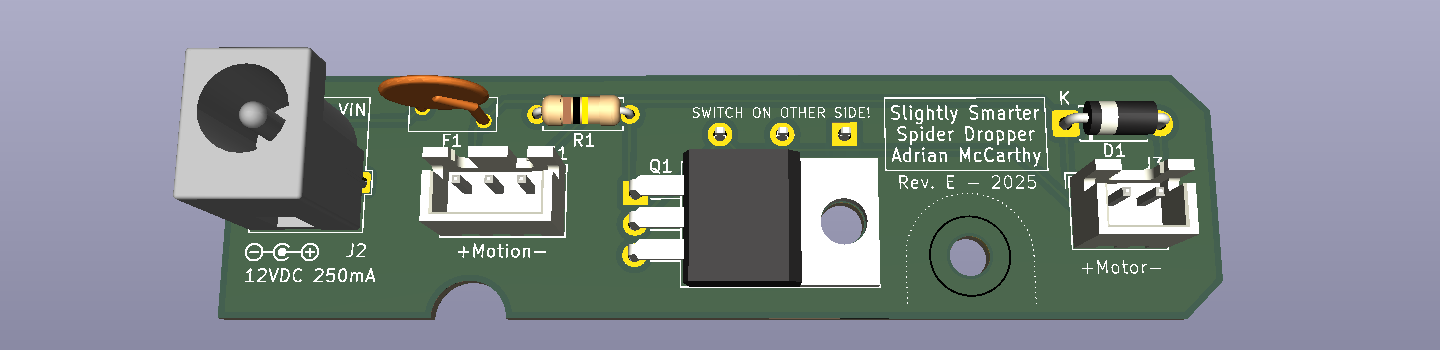
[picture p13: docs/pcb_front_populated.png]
Populated circuit board


- [ ] Solder the microswitch into position on the opposite side of the board.

> Tip:  Use the soldering jig (`#3D`) to hold the microswitch in place while soldering.  Place the switch on the board and slip the jig over it. With the board flush with the jig, turn them both over and set it flat on your worksurface. Solder one terminal of the switch while applying some downward pressure to keep the board against the jig and the switch pressed.  Check that the switch is straight before soldering the other two terminals.

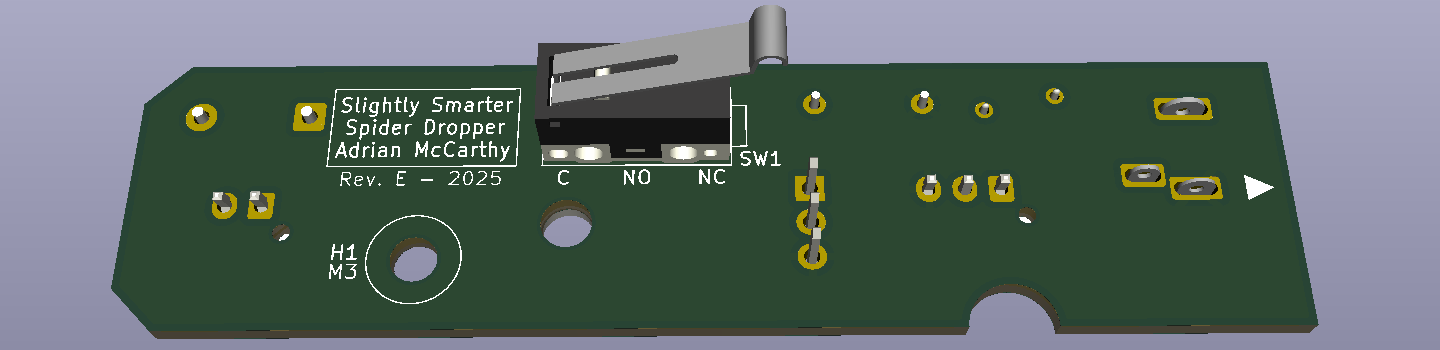
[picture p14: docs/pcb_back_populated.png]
Switch installed on back of circuit board
<br>
Note:  The lever of the switch is smaller than shown in the illustration above.

### Attach the Circuit Board (`#SSSD-UP` only)

- [ ] Match the triangular arrow on the circuit to the one embossed on the build plate and slide that end under the lip.
- [ ] Secure the circuit board with an M3×6mm screw at H1 and a square nut in the pocket underneath.

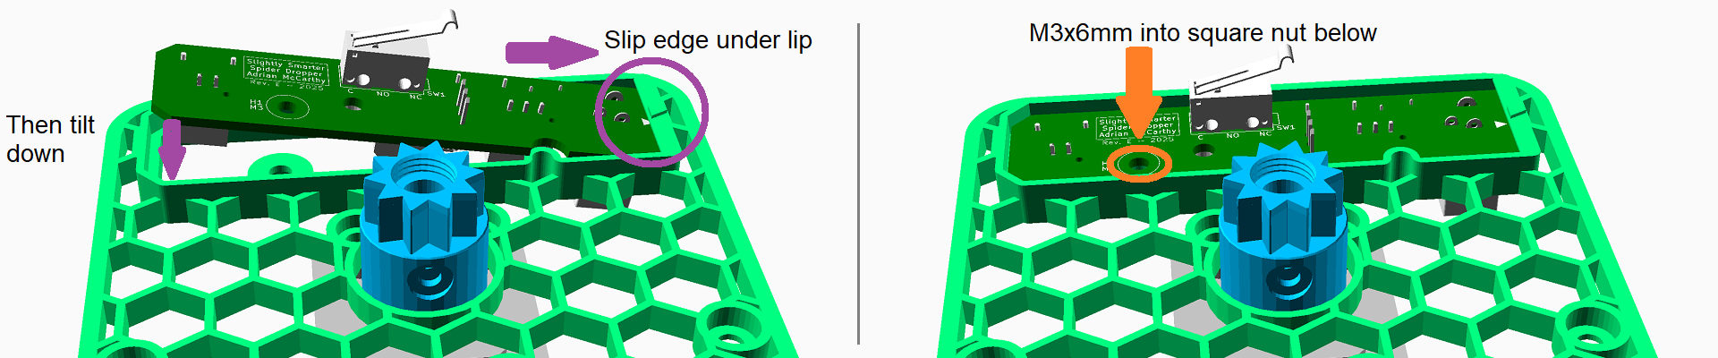
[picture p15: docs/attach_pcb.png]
Attaching the circuit board


- [ ] Plug the motor pigtail into the 2-pin connector on the circuit board.
- [ ] Secure the pigtail to the base plate with a small zip tie as shown.

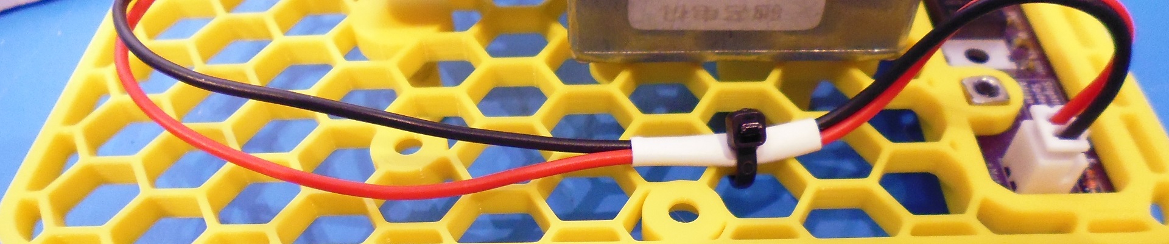
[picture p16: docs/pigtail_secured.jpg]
Motor Pigtail Secured with zip tie


### Make the Sensor Cable (`#SSSD-UP` only)

- [x] Remove ~50&nbsp;mm (2&nbsp;inches) of the jacket from one end of the cable.
- [x] Strip ~2&nbsp;mm from the tips of each of the exposed wires.
- [x] Crimp the JST XH pins (female) onto the wires.
- [x] Insert the pins into the JST XH housing in **RED/YELLOW/BLACK** order, with RED next to the notch in the housing.
- [x] Slide ~25&nbsp;mm (1&nbsp;inch) of heat-shrink tubing over the cable and shrink it ~75&nbsp;mm (3&nbsp;inches) from the connector.

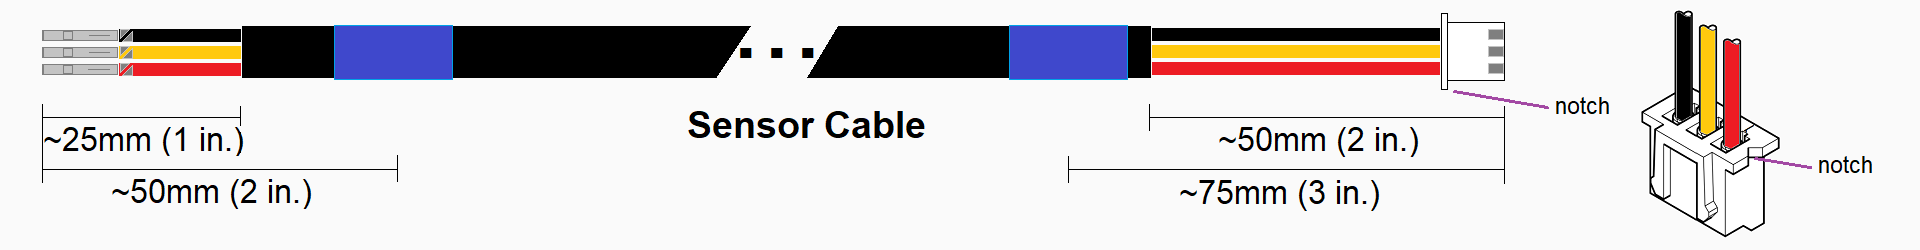
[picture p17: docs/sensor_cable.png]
Sensor cable


- [x] Remove ~25&nbsp;mm (1&nbsp;inch) of the jacket from the other end of the cable.
- [x] Strip ~2&nbsp;mm from the tips of each of the exposed wires.
- [x] Crimp the Dupont-style pins (female) onto the wires.  Do not put them into the connector housing yet.
- [x] Slide ~25&nbsp;mm (1&nbsp;inch) of heat-shrink tubing over the cable and shrink it ~50&nbsp;mm (2&nbsp;inches) from the tips of the pins.

### Connect the Motion Sensor (`#SSSD-UP` only)

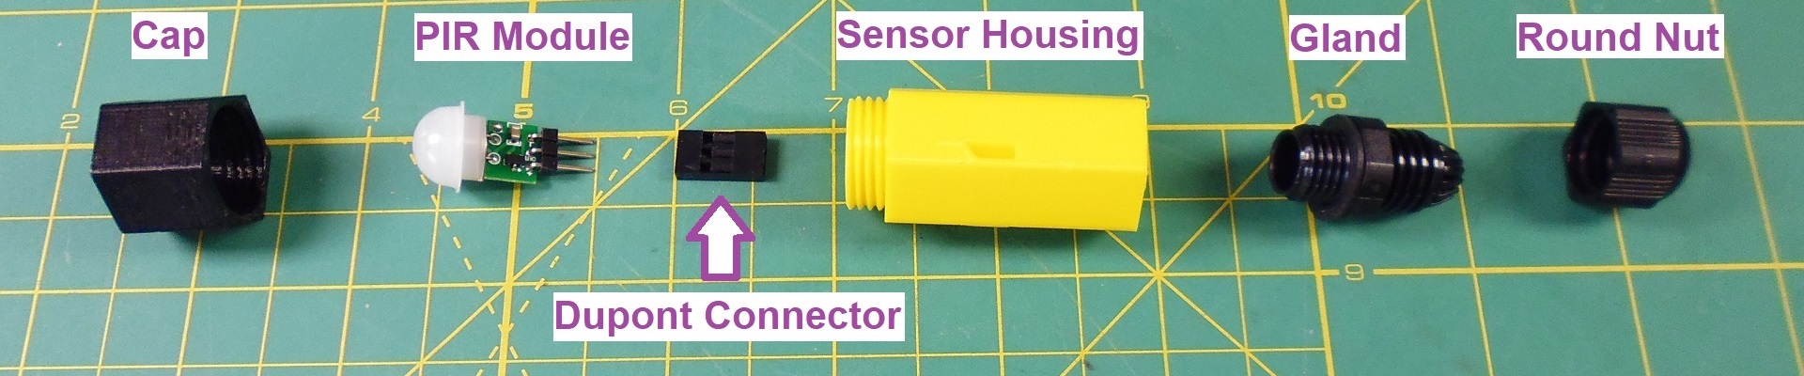
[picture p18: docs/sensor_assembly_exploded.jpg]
Motion Sensor Assembly


- [x] Remove the flat nut from the cable gland.  You won't need it.
- [x] Screw the gland into the back of the 3D-printed sensor housing.

> Tip:  Tighten and loosen the gland to the housing a few times to clear out the threads.

- [x] Remove the round nut from the cable gland.
- [x] Slip the Dupont pins into the rounded end and let the nut slide up the cable.
- [x] Feed the Dupont pins into the gland.

> Tip:  Be careful not to dislodge the rubber seal held at the tips of the fins in the cable gland.

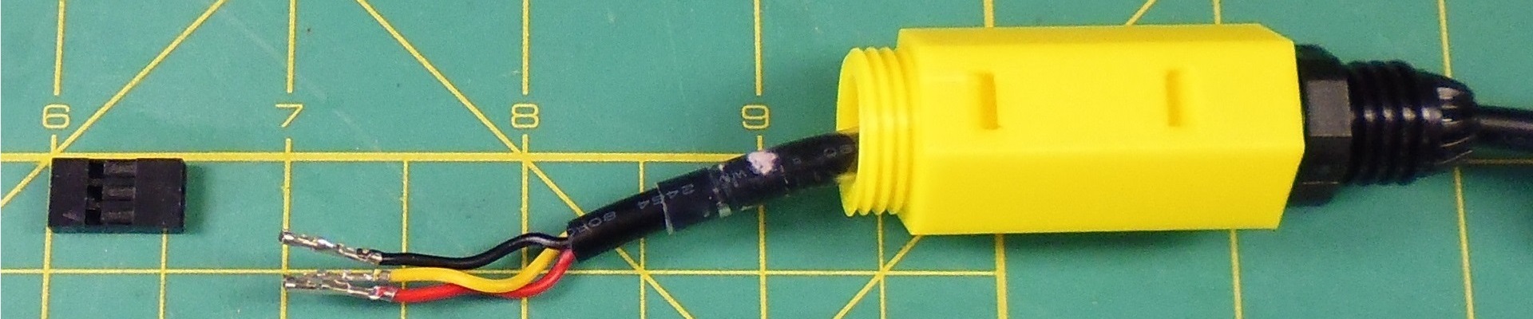
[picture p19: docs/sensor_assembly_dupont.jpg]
Progress: Cable through sensor housing


- [x] When the pins extend out the top of the sensor housing, insert them into the Dupont connector body in **RED/YELLOW/BLACK** order.

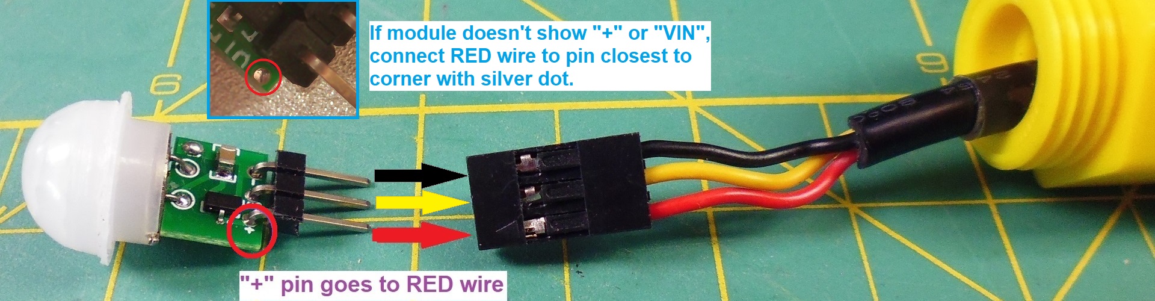
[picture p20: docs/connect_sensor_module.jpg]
"+" pin goes to red wire


- [ ] Insert the PIR module into the connector, ensuring that the pin marked **`+`** or **`VIN`** corresponds to the **RED** wire.

> Tip:  If the dome pops off the PIR module, be careful not to touch the exposed sensor.  Replace the dome and hold it in place until the module is secured in the housing.

- [ ] Push gently on the dome of the PIR module until the brim is flat against the rim of the housing.

> Tip:  You'll need to guide the excess cable out through the gland as you push the sensor into the housing, but do not pull the cable so hard that it could pull the connector from the sensor module.

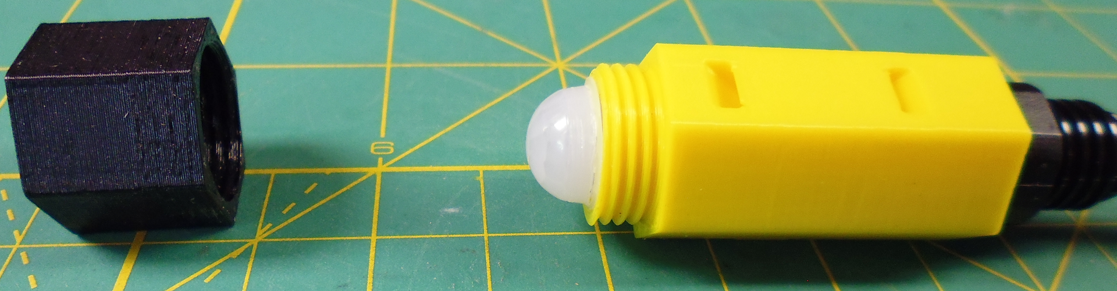
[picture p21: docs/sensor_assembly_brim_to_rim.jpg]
Brim of sensor dome is flat against the rim of the housing


- [ ] Screw the cap onto the sensor housing.
- [ ] Tighten the round nut onto the cable gland.

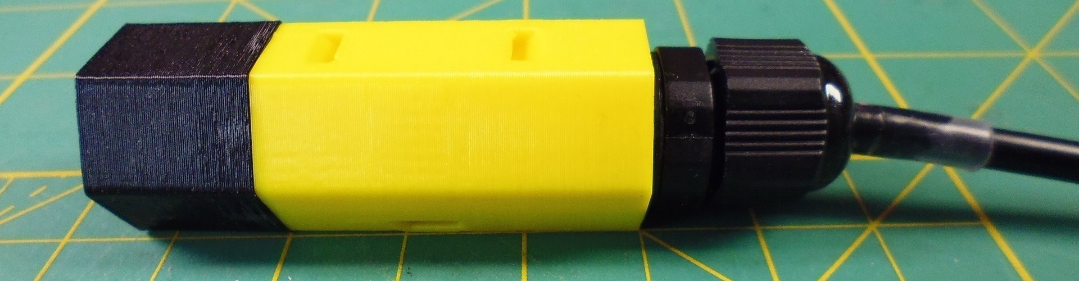
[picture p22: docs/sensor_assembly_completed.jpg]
Completed sensor assembly


- [ ] Set the sensor cable aside for now.

### Install the Spool

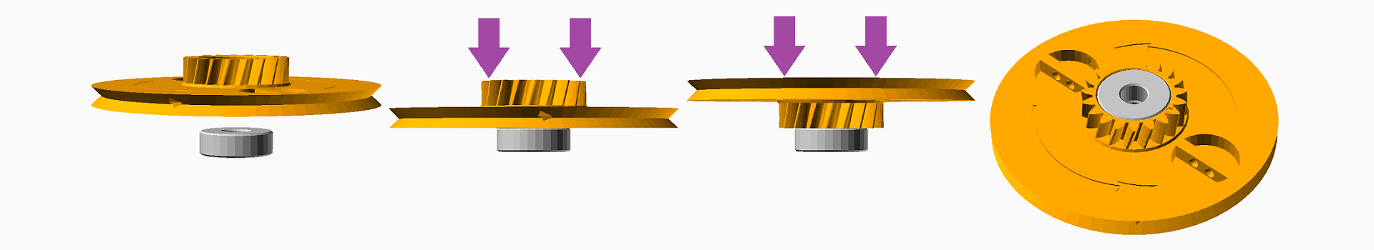
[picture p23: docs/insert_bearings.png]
Inserting the bearings


- [ ] Place one bearing on a strong, flat surface.
- [ ] Position the wide face of the spool over the bearing and press down firmly until the bearing is inside the bore.
- [ ] Invert the spool and repeat with the second bearing.
- [ ] Slide the spool onto the axle so that the wider part is closer to the base plate.

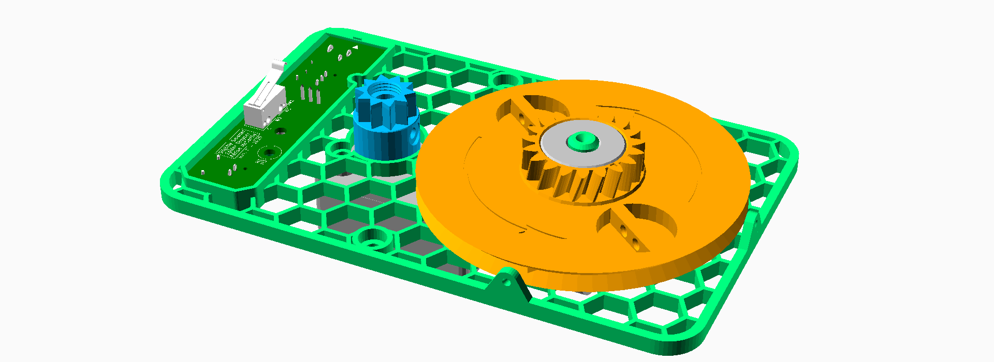
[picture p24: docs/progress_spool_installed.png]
Progress: Spool installed


### Install the Drive Gear

- [ ] Press the drive gear onto the shaft adapter so that the toothless section is closest to the spool gear.
- [ ] Confirm that the flat surface of the gear is flush with the top of the shaft adapter.
- [ ] Turn the spool and confirm it doesn't rub against the drive gear.
- [ ] Screw the hub screw into the shaft adapter and hand tighten.

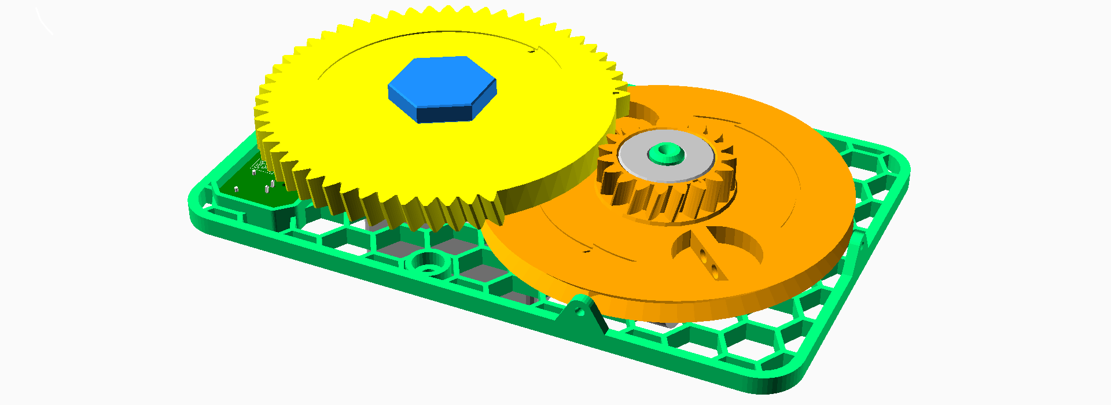
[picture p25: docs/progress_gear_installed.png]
Progress: Drive gear installed


### Attach the Monofilament (Fishing Line)

The base plate has two string guides at the edges near the spool.  Decide whether you will hang the mechanism horizontally or vertically.  You will use the guide that's below the spool when hanging.

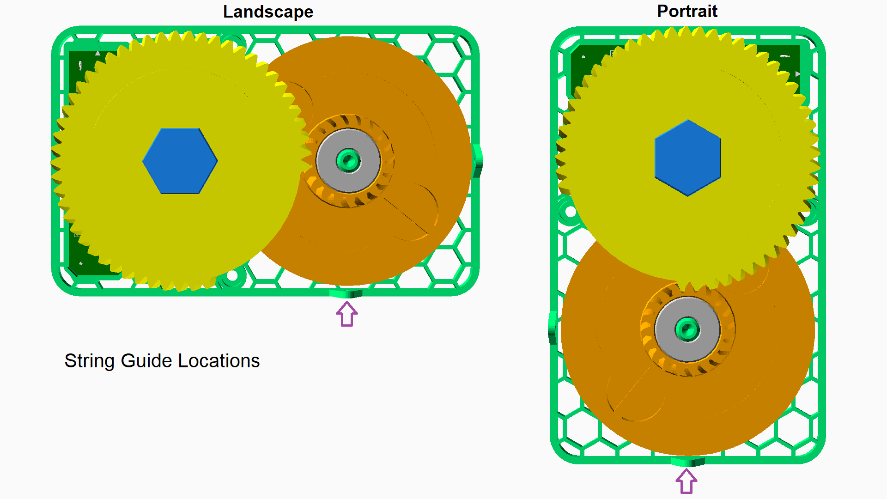
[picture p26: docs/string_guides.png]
Locate the string guide for your orientation


- [ ] Feed one end of the monofilament through the guide toward the spool.
- [ ] Thread the monofilament into one of the holes along the edge of the spool.
- [ ] Loop the monofilament through the two holes in the bar that divides the recess.
- [ ] Tie the line to itself.
- [ ] Trim the excess and ensure the knot remains entirely within the recess.

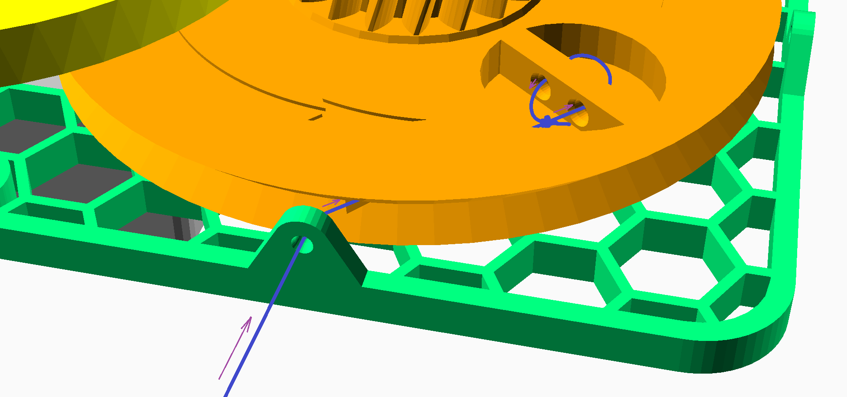
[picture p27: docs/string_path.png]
Line Routing


### Prepare the Spider

To make the toy spider hang realistically ...

- [ ] Trim a short zip tie about 12 mm (1/2 inch) down from the end with the loop.
- [ ] Select a drill bit that's about as wide as the zip tie.
- [ ] Carefully drill a hole in the back of the spider's abdomen (near the spinnerets) and toward its center of mass.  The hole needn't be deeper than the trimmed zip tie is long.
- [ ] Dip the zip tie in a blob of hot glue (use the black "cosplay" glue if you can).
- [ ] Insert the zip tie into the hole so that only the loop protrudes.  Ideally the glue should fill any gap between the zip tie and the sides of the hole.
- [ ] Allow the hot glue to cool, then check that the zip tie is secure.

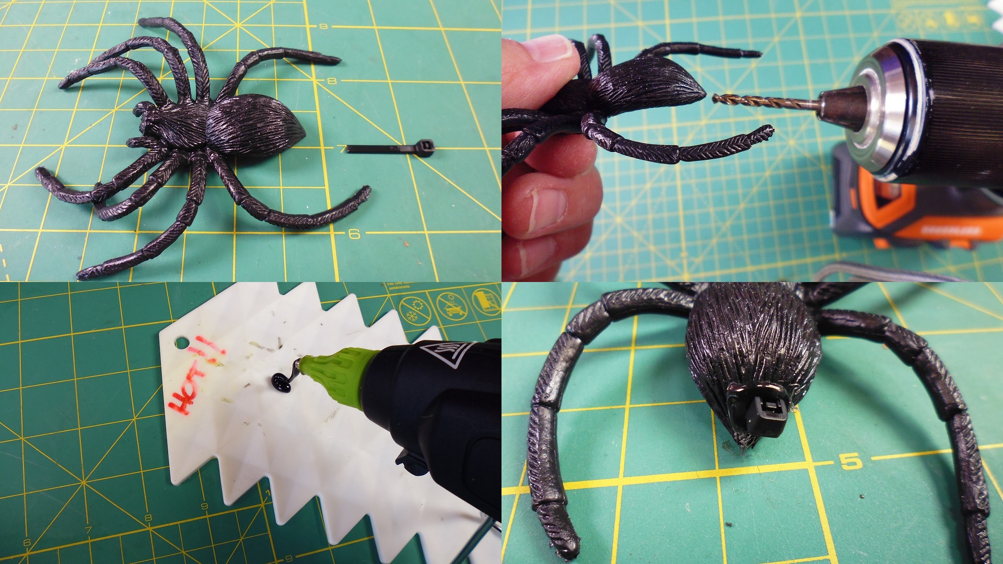
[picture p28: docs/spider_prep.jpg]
Prepare the spider


> Tip:  It's a great time to paint and/or flock your spider.

### Attach the Spider

There must be at least 24 inches (610 mm) of line between the bottom of the string guide and the point where the spider is tied.

- [ ] Tie the free end of the monofilament to the spider through the loop in the zip tie.
- [ ] Keeping some tension on the string, wind the spool 2.5 revolutions in the direction shown by the arrows.  If the spider reaches the guide before you complete the turns, the spider was tied too high.
- [ ] Trim the excess monofilament.

### Final Connection (`#SSSD-UP` only)

- [ ] Plug the sensor into the 3-pin connector on the circuit board.
- [ ] Use a small zip tie to secure the cable to the base plate as shown.

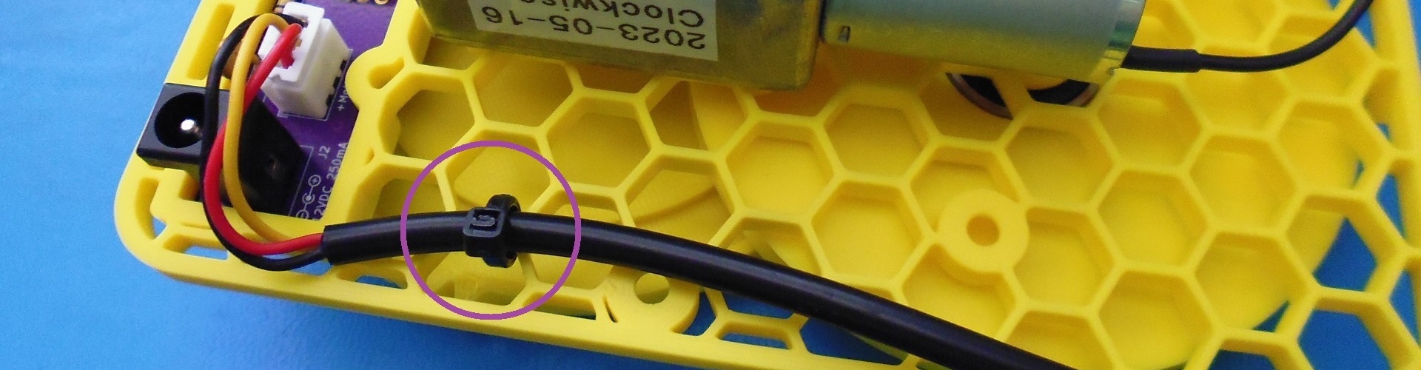
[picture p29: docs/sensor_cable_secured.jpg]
Sensor cable secured with zip tie


### Test the Mechanism

- [ ] Check the alignment by viewing the mechanism from the edge, as shown.

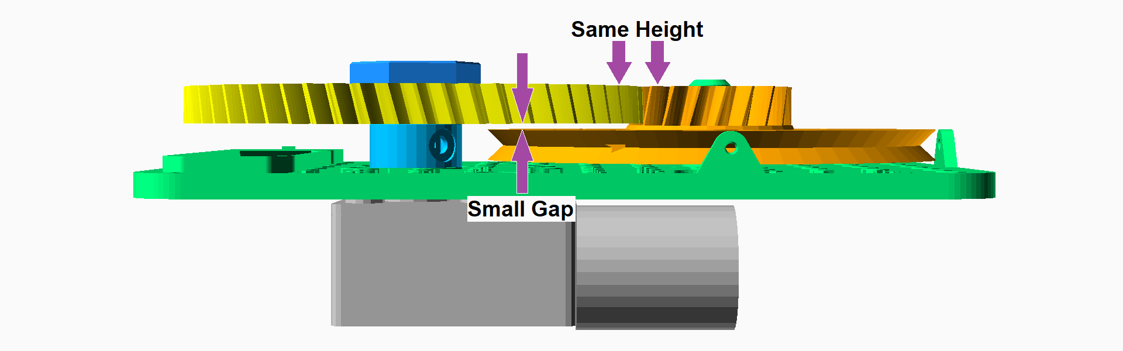
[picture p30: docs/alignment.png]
Alignment check


- [ ] Hang the mechanism from above with two zip ties, as shown.

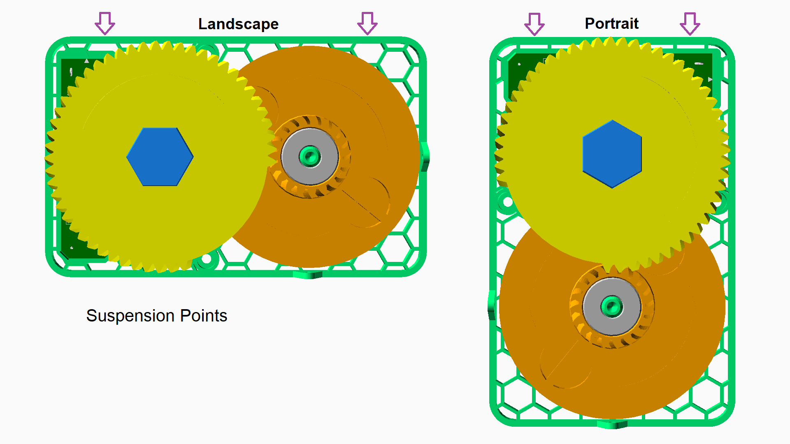
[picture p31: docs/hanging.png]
Suspension Points


- [ ] Allow the spool to fully unwind and the spider to dangle.
- [ ] Connect the power.

`#SSSD-AC`/`#SSSD-DC`:  The spider should rise and then drop suddenly.  The cycle should repeat continuously.

`#SSSD-UP`:  The spider should rise to its highest point, and then stop until the sensor detects motion.  When that happens, the spider will drop suddenly and then rise again.

- [ ] Confirm the line winds in an orderly fashion around the spool.
- [ ] Confirm the drive gear doesn't rub against the spool.
- [ ] Confirm the spider drops the full amount.
- [ ] Allow the mechanism to run for several cycles to ensure it is not prone to jamming.

## Happy Haunting

Congratulations!  You've completed assembly of the Stupidly Simple Spider Dropper.

Consult the User Guide to learn how to set up and operate your spider dropper safely.

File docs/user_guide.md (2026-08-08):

# Stupidly Simple Spider Dropper<br>User Guide

Adrian McCarthy 2026 for the [Northern California Haunters Group](https://www.norcalhaunters.com/)

Source files and documentation available at https://github.com/aidtopia/spider_dropper

## Setup

1.  Hang the mechanism from above using zip ties through the openings at the very edge of the honeycomb plate.  (If it can swing a little bit, that's actually good.)  You can hang it in landscape or portrait orientation to suit your space, just make sure the string runs through the guide on the edge closest to the floor.  Make sure the hooks or zip ties do not interfere with the mechanism.

orientations Orientation Options

2.  **Before** connecting power, ensure that the string is either wound properly around the spool or completely unwound.  If any part of the string is wrapped around the axle, a gear, or anywhere else, free it up first.  (See [Jams](#jams) below.)

3.  The spider **must** be able to drop its full distance without interference.

    * Don't try to have it "land" on something.
    * Don't drop it near decorations that it could get tangled in.
    * Don't drop it on guests' heads.

## Motion Sensor

If your model does not have a motion sensor, this section does not apply.

When you first apply power, the mechanism will run up to one full cycle until the spider is in the standby position.

When the motion sensor detects someone, the spider will drop and then climb back up to the standby position.  The entire cycle takes about 10 seconds.  The cycle repeats when motion is detected again.  If there's constant motion, the cycle will just keep running.

Secure the motion sensor to something rigid.  The housing has slots that accommodate zip ties for this purpose.  If you attach it to a fence that gets bumped or that shakes in the wind, you'll get false triggers.

The cap over the motion sensor can be unscrewed and swapped for alternate ones that change the detection zone.  You probably want to keep the one with the smallest hole, called "the snoot".  If that's still too sensitive, you can place one piece of cellophane tape (e.g., Scotch tape) across the small hole.  A good way to limit the detection zone is to mount the sensor overhead and aimed straight down.

## Jams

If the spider fails to drop the full distance, the mechanism will likely jam on the next cycle.

If you detect a jam early and disconnect the power, you can probably free it up before there's any damage.

If the jam persists, the motor could overheat.  To avoid that, the 3D-printed shaft adapter is designed to be a sacrificial part.  Under the constant strain of a jam, it will deform, allowing the motor to run freely without actually driving the mechanism.  If this happens, the mechanism can be repaired by replacing the shaft adapter.  See the Assembly Instructions for details.

If your model has the "Slightly Smarter" upgrade, the circuit has a fuse.  If it gets too hot, it will cut the power to the motor.  When the fuse cools again, it will automatically reset.  You don't need to replace the fuse or do anything to reset it other than give it time to cool off.  (If it cools off before the jam has been cleared, it may cut the power again.)

With these protections in place, it should be fine to let the spider dropper run unattended.  In the worst case, the spider will simply stop dropping, but the motor should not overheat.

## Clearing a Jam

1.  Make sure the power is disconnected.

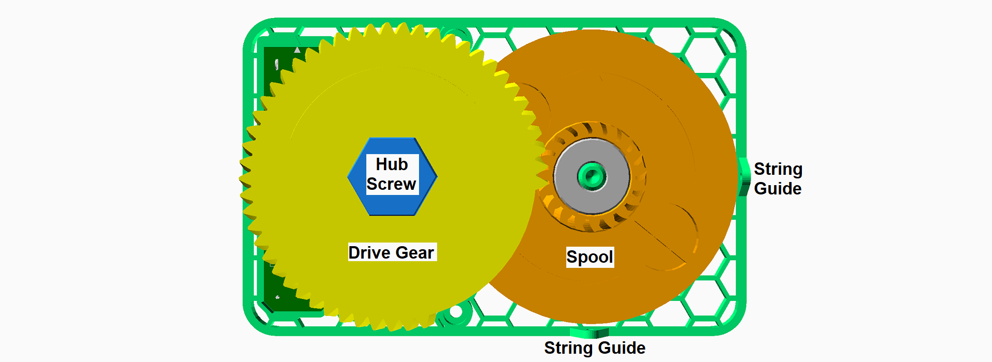
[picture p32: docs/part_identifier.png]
parts identifier Main Parts


2.  Remove the hub screw.

3.  Pull the drive gear off the shaft adapter.

4.  Pull the spool off its axle.  (It may be tight.  Don't wiggle, just pull it straight.)

5.  Free up the monofilament line.  If it's kinked, replace the line.

6.  If the shaft adapter has deformed, replace it.  (If you can rotate it around the motor shaft with the set screw(s) tightened, it's a goner.)

    To remove the old shaft adapter, loosen the set screw(s) and remove the shaft screw (the one that goes into the end of the shaft).  Print a new adapter.  Insert the nut(s) or heat-set threaded insert(s) and then the set screws.  Slide the adapter over shaft as far as it will go.  Tighten the set screw(s) against the flat side(s) of the shaft.  Screw shaft screw through the end of the adapter into the end of the shaft.

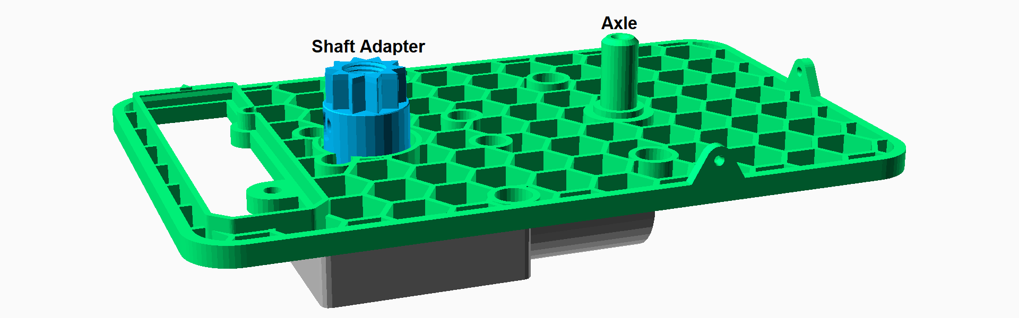
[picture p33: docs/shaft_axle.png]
shaft adapter and axle Shaft Adapter and Axle


7.  Push the spool back onto the axle.  Make sure it's on all the way.  When you look at it from the edge, it should be perfectly parallel to the honeycomb plate, and the string guide holes should be perfectly centered with the center of the spool.

8.  Make sure the string is completely unwound and pulled as far as possible through the string guide.

9.  Slide the drive gear onto the shaft adapter so that the portion without teeth is closest to the small gear.  Check it from the edges.  The drive gear should be perfectly parallel with the honeycomb plate.  There should be a slight gap between the spool and the drive gear.  And the top edges of the two gears should be aligned.  Secure the drive gear with the hub screw.

alignment Edge View Showing Alignment

10.  With the mechanism suspended, and the spider at its lowest position, reconnect the power.  Run it through a couple cycles to make sure there are no obstructions to a full drop.

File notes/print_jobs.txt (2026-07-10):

sssd_ac_coarse              (base plate, drive, spool)
sssd_dc_coarse              (base plate, drive, spool)
sssd_up_coarse              (base plate, drive, spool)

sssd_ac_coarse_with_tools   (base plate, drive, spool, bearing tool)
sssd_dc_coarse_with_tools   (base plate, drive, spool, bearing tool)
sssd_up_coarse_with_tools   (base plate, drive, spool, bearing tool, soldering jig)

sssd_ac_fine                (7mm adapter, cap screw)
sssd_dc_fine                (6mm adapter, cap screw)
sssd_up_fine                (6mm adapter, cap screw, PIR housing)
sssd_up_fine_with_tools     (6mm adapter, cap screw, PIR housing, pin bender)

sssd_ac_thin_nut_fine       (7mm adapter, cap screw)
sssd_dc_thin_nut_fine       (6mm adapter, cap screw)
sssd_up_thin_nut_fine       (6mm adapter, cap screw, PIR housing)
sssd_up_thin_nut_fine_with_tools
                            (6mm adapter, cap screw, PIR housing, pin bender)

sssd_ac_heatset_fine        (7mm adapter, cap screw)
sssd_dc_heatset_fine        (6mm adapter, cap screw)
sssd_up_heatset_fine        (6mm adapter, cap screw, PIR housing)
sssd_up_heatset_fine_with_tools
                            (6mm adapter, cap screw, PIR housing, pin_bender)

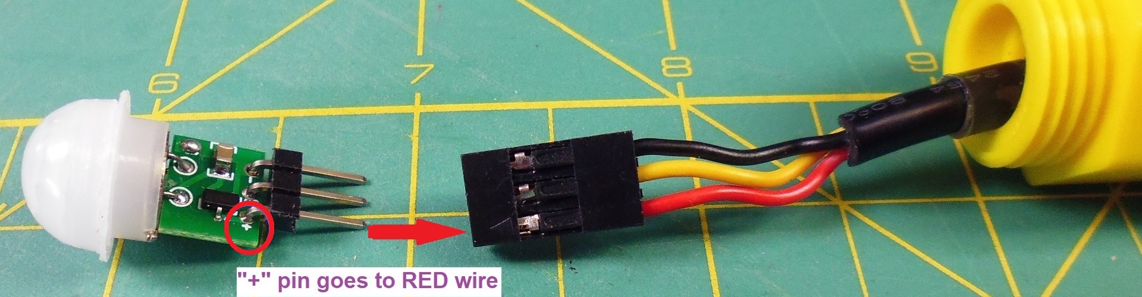
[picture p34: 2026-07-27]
docs/sensor_assembly_cable_terminated.jpg

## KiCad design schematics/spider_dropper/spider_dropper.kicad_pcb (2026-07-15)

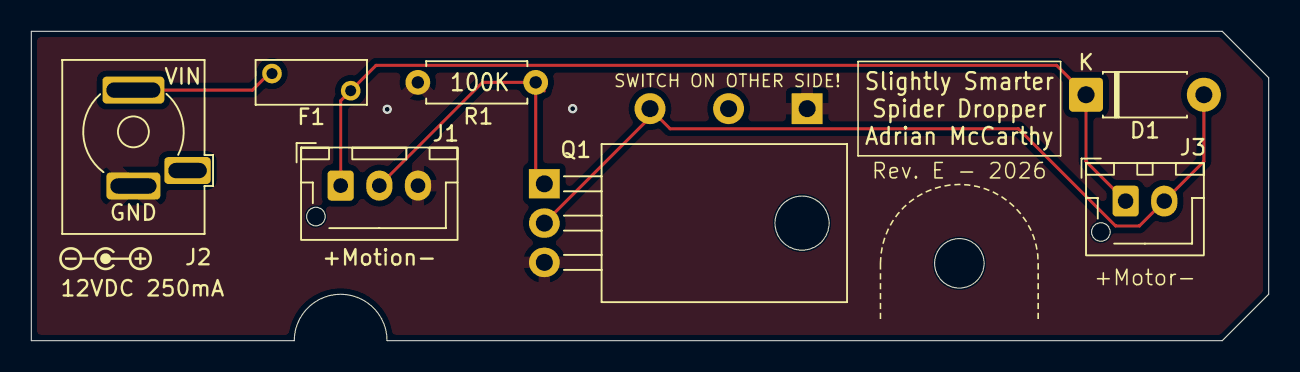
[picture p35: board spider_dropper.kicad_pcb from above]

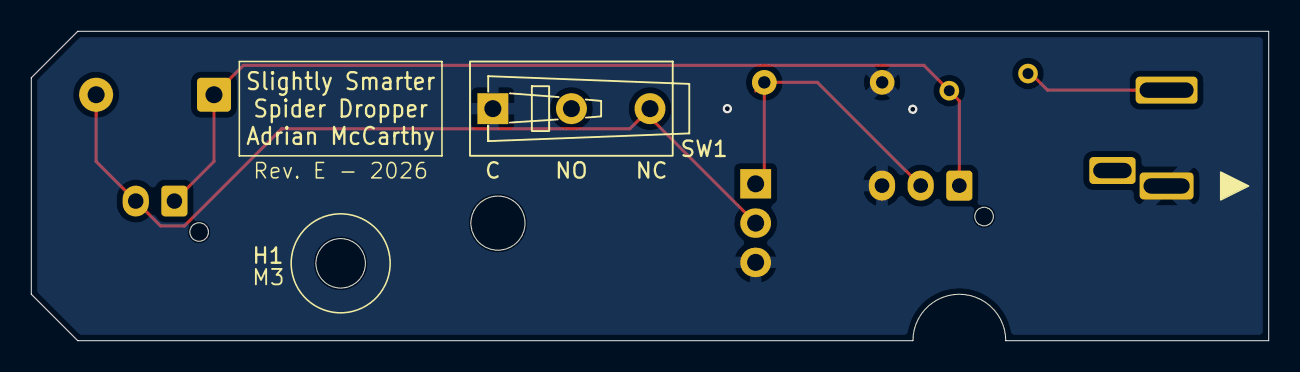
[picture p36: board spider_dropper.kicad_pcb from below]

Board: 2 copper layers, 80.0 x 20.0 mm, 10 parts (2 on the bottom side), 5 nets.

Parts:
D1: 1N4001; D_DO-41_SOD81_P7.62mm_Horizontal
F1: PTC 250mA; Fuse_BelFuse_0ZRC_L7.4mm_W3.1mm
G1: PolarityCenterPositive; PolarityCenterPositive_6x1.5mm_Silkscreen
H1: M3; MountingHole_3.2mm_M3
J1: JST_XH_3; JST_XH_B3B-XH-AM_1x03_P2.50mm_Vertical
J2: PJ-044AH; BarrelJack_SameSky(CUI)_PJ-044AH
J3: JST_XH_2; JST_XH_B2B-XH-AM_1x02_P2.50mm_Vertical
Q1: IRLZ34N; TO-220-3_Horizontal_TabDown
R1: 100K; R_Axial_DIN0207_L6.3mm_D2.5mm_P7.62mm_Horizontal
SW1: ZX40E20C01; SW_SPDT_THT_ZX_Microswitch_P5.08mm

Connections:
+12V: F1.1, J2.1
/MOTION: J1.2, Q1.1 (G), R1.1
/MOTOR+: D1.1 (K), F1.2, J1.1, J3.1
/MOTOR-: D1.2 (A), J3.2, Q1.2 (D), SW1.3 (A)
GND: J1.3, J2.2, Q1.3 (S), R1.2, SW1.1 (B)

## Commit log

2024-11-29 Capture the current schematics in the new repot.
    [spider_dropper.kicad_pcb, spider_dropper.kicad_sch]
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2024-11-30 Re-oriented and re-position the PCB and cradle.
    Also gave each printed part a unique color in preview.
    Rev A boards ordered from this commit.
    [spider_dropper.kicad_pcb, spider_dropper.scad]
2024-12-01 Carved space for the limit switch out of the drive gear.
    Instead of moving the gear and spool outwards, I thinned out a channel
    in the drive gear to accommodate the natural height of the limit switch.
    [hub_adapter.scad, spider_dropper.scad]
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2024-12-10 Made adjustements to the cradle.
    With the Rev A PCBs in hand, I discovered that the screw heads holding
    the cradle would interfere with the power and motor connectors, so I
    moved them inward.
    I also extended the "index" pin on the cradle up through the base plate
    to ensure proper orientation of the PCB.
    The cradle is too flimsy. I plan to address that soon.
    [spider_dropper.scad]
2024-12-10 JGY motor shaft uses M3 not M4 hub screw.
    This was probably a copy-modify-paste error from the deer motor,
    long, long ago.
    [spider_dropper.scad]
2024-12-10 Removed (most of) the instructions from the SCAD file.
    [spider_dropper.scad]
2024-12-10 Fixed distance to limit switch.
    [spider_dropper.scad, spider_dropper_parts.xlsx]
2024-12-11 Applied more tweaks to the cradle.
    Tried to stiffen it up and improve the mounts.
    [spider_dropper.scad]
2024-12-15 Experimenting with a better cradle and a limit switch mounting block.
    The cradle was twising easily, and, since it's only screwed in from
    one side, the other long edge was drooping. This is an attempt to
    beef-up the cradle to prevent that.
    I got feedback that having the limit switch soldered directly to the
    PCB might cause strain on the PCB that could reduce its lifetime, so I
    also started designing a mounting block to hold the limit switch. The
    idea is to make the precise position adjustable with screws.
    [spider_dropper.scad]
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2024-12-22 Fixed a bug and experimented with a mounting block for the limit switch.
    The bug occurred when the width of the groove in the spool became
    negative, causing the polygon profile of the spool to have a whole,
    which prevented OpenSCAD from generating a valid mesh.
    I considered removing the limit switch from the PCB over concern that
    the repeated action might stress the PCB, shortening it's life. I
    started designing a way to mount the switch (in a different orientation)
    to detect the gap in the drive gear teeth. The idea was the mount the
    switch to a block that could be positioned along some rails at assembly
    time to ensure it was in exactly the right position. This got overly
    complicated an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
    [spider_dropper.scad]
2024-12-22 Updated PCB layout (now Rev. B) for more clearance around connectors.
    The motion sensor header was within the margin, but the motion sensor
    itself would run into the edge of the deeper cradle. I centered it
    on the short axis and aligned it with the index post on the long axis.
    This should enable the cradle to have some supports for the sensor
    module or a cable that connects to it.
    [spider_dropper.kicad_pcb]
2024-12-22 Made the PCB cradle a little shorter.
    It should still be comfortably taller than the connectors, while
    reducing the conflict between the motion sensor and the wall of
    the cradle.
    To ensure good slicing results, I fudged the height of the holes for
    power and motor wires passing through the wall of the cradle.
    [spider_dropper.scad]
2024-12-23 Reduced the depth of the nut pockets in the cradle to ease assembly.
    Also tweaked the power connector hole for a stronger print.
    [spider_dropper.scad]
2024-12-24 More PCB layout tweaks to ease assembly.
    Power connector is closer to cradle wall so that there's enough room
    for a fat plug.
    Fuse and TIP120 are in a little more from the edges.
    Resistors and BJT are shifted to space out the pads for easier
    soldering.
    [spider_dropper.kicad_pcb]
2025-01-12 Changed PIR connector to JST XH, which is keyed and holds securely.
    [spider_dropper.kicad_pcb, spider_dropper.kicad_sch]
2025-01-12 Switched the JST XH footprint to one with hole for "boss".
    The boss is for alignment and possibly additional support. This
    footprint is compatible with the connector that doesn't have a boss.
    [spider_dropper.kicad_pcb, spider_dropper.kicad_sch]
2025-08-13 Tried to do circuit simulation in KiCad. Not working yet.
    The Spice models are from manufacturer OnSemi's website.
    [spider_dropper.kicad_pcb, spider_dropper.kicad_sch]
2025-08-13 Removed the unused switch mounting block from the SCAD design.
    [spider_dropper.scad]
2025-08-15 Modified one dimension to improve motor mount strength.
    deer_base_d is the diameter of the cutout to accommodate the raised
    area on the face of a reindeer motor. Making this slightly smaller
    allowed more "meat" around the mounting holes for a JGY motor without
    compromising the fit for the reindeer motor.
    [spider_dropper.scad]
2025-08-15 Added current-limiting resistor to base of Q2.
    With the thermal camera, I happened to notice that Q1 was heating up
    more than I expected. When on, it was passing almost 11mA. Within
    spec, but way more than necessary to turn on Q2. Added a current
    limited resistor to the base of Q2 dropped the current (and power)
    through Q1 to less than 1mA.
    Made additional layout tweaks to PCB and updated markings to Rev C.
    [spider_dropper.kicad_pcb, spider_dropper.kicad_sch]
2025-08-27 Redesign of slightly smarter PCB.
    Simplified by using a MOSFET, which requires fewer parts and runs the
    motor more efficiently. Since I'm also working on a re-do of the
    printed parts, I went ahead and changed the layout and mounting options
    for the board. That makes the new PCB incompatible with the old
    mechanical design.
    [spider_dropper.kicad_pcb, spider_dropper.kicad_sch]
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2025-08-29 Checkpoint on version 2 parts.
    Base plate is feature complete.
    [spider_dropper2.scad]
2025-08-29 Checkpoint latest version of Rev D schematic and PCB.
    [spider_dropper.kicad_pcb, spider_dropper.kicad_sch]
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2025-08-31 Added better splines to shaft adapters and drive gear.
    [spider_dropper2.scad]
2025-08-31 Needed a tighter fit on the splines.
    [spider_dropper2.scad]
2025-08-31 Got 3D models for the JST connectors to appear in rendering.
    I'm using the KiCad-provided models for the connectors without the
    extra alignment nubs. But I didn't want to switch the footprint
    because I want the PCB to have the holes for those nubs.
    [spider_dropper.kicad_pcb]
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2025-08-31 Fixed size of PCB mounting tab and added a nut pocket.
    [spider_dropper2.scad]
2025-08-31 Added alternate string guide and incremental bridging for nut pocket.
    [spider_dropper2.scad]
2025-08-31 Updated comments and started reconstructing the assembly preview.
    [spider_dropper2.scad]
2025-08-31 Started updating and re-integrating the spool assembly.
    Also fixed plate_l to accomodate gap for the alternate string guide.
    [spider_dropper2.scad]
2025-09-02 I think I'm ready to order Rev. D PCBs.
    [spider_dropper.kicad_pcb, spider_dropper.kicad_sch]
2025-09-03 Made the shaft adapter beefier; improved tie-off for string to spool.
    When the mechanism gets jammed up, the shaft adapter was failing a
    little easier than it should.
    The current way of securing the string to the spool works, but I have
    ideas for making it better.
    [spider_dropper2.scad]
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2025-09-04 Made a spreadsheet to better understand the sizing contraints.
    The parameterization of the drop distance is very limited because the
    SCAD code doesn't currently adjust the tooth counts or gear ratios.
    Adjusting the diameter of the spool can only go so far until you hit
    a constraint.
    [gear_ratios.xlsx]
2025-09-04 Improved tie-off for the string on the spool.
    This works well, but there's still room for improvement.
    Also computed the minimum tooth counts for the gears in preparation for
    improved parameterization. The computed values match the ones that
    have been hardcoded for a long time now.
    [spider_dropper2.scad]
2025-09-06 Added the spool guard and redesigned the axle.
    [spider_dropper2.scad]
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2025-09-07 Added a cap screw to hold the drive, and adjusted the new axle.
    The cap screw kinda works when printing with 0.3mm layers, but it
    would work better at 0.2mm. It's essentially a 1/4"x20 bolt. In a
    pinch you can force in a tripod mounting screw.
    I'd gotten to a nice fit with a prototype axle, but when it was printed
    as part of the base plate, the shrinkage was different and thus the
    spool assembly didn't fit at all. After more experimentation, I dialed
    in a reasonable default for the "fudge" value to control the tightness.
    I'm still not convinced it'll work for everyone given differences in
    machines, slicers, materials, etc. I'm considering making it a
    separate part that attaches to the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
    [spider_dropper2.scad]
2025-09-11 Updated PCB layout to Rev E.
    Rev D was usable, but I discovered:
    * The footprint for the vertical power jack was wrong. I corrected it
    in my footprint library and updated the PCB layout accordingly.
    * The diode was a bit close to the cut corner. I nudged it in to make
    it easier to solder in place.
    [spider_dropper.kicad_pcb, spider_dropper.kicad_sch]
2025-09-12 Another fix to shaft adapters (and cap screw).
    Recent changes prevented the shaft adapter from sliding all the way
    down to the JGY motor base, which meant the drive gear was too high
    and wouldn't depress the switch on the Slightly Smarter PCB.
    Fix was to make the cap screw diameter larger than the shaft diameter.
    To get good threads, the adapter and the cap screw require 0.2mm layers
    (or better). The rest of the parts can still be printed with 0.3mm.
    Now it's almost too close, as the switch lever drags in the channel on
    the drive gear. I can look at that later.
    This commit also includes a little code cleanup.
    [spider_dropper2.scad]
2025-09-12 Changed PCB model to accept a limit for the switch position.
    This was helpful in debugging a clearance and dragging issue.
    [spider_dropper2.scad]
2025-09-15 Made more tweaks to the build plate.
    Added a pocket to hold the end of the PCB near the power connector. It
    has a drooping bridge and needs some sort of support.
    Turned off the spool guard experiment. It doesn't help.
    Tried again to make a tighter fitting axle. This works better, but the
    variation from print-to-print means it won't always be better.
    [spider_dropper2.scad]
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2025-09-21 Several improvements.
    * Abandoned the ribbed axle and might a tight, strong one like before.
    * Added a module to generate text axles.
    * Added a bridge to capture the end of the PCB to reduce flexing.
    * Added a jig to hold the switch in position while soldering it.
    * Added a bearing pusher tool.
    * Used the KiCad-generated STL for visualizing the PCB.
    * Improved the print layout code.
    [spider_dropper2.scad]
2025-09-21 Small improvements for Rev. E.
    * Moved the connectors to make it easier to connect & disconnect.
    * Moved the diode in from the corner.
    * Added detail to the perimeter boundary (in User Drawings layer).
    * Added a triangular arrow to assist with alignment in assembly.
    [spider_dropper.kicad_pcb]
2025-09-21 Changed the diode footprint to a DO-41.
    The leads of the 1N4001 diodes I have barely fit into the holes for the
    default footprint. Datasheet suggests DO-41 is the correct package,
    and KiCad has a footprint for that with the same spacing but larger
    holes.
    [spider_dropper.kicad_pcb, spider_dropper.kicad_sch]
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2025-09-28 Switched to smaller, cheaper signal diode.
    The 1N4001 was overkill for the motor flyback. The 1N4148 is a common
    signal diode that fits the space a little better.
    Also nudged the connector for the motor controller to help my fat
    fingers access it.
    [spider_dropper.kicad_pcb, spider_dropper.kicad_sch]
2025-10-15 Reverted change to the diode. Back to 1N4001.
    [spider_dropper.kicad_pcb, spider_dropper.kicad_sch]
2026-04-30 Added Customizer option for thin square nuts (recommended).
    [spider_dropper2.scad]
2026-05-09 Customizer now allows heat-set inserts for shaft adapter set screws.
    [spider_dropper2.scad]
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2026-05-27 Improved the PCB model visualization in OpenSCAD.
    Added batch file that generates two STL models from the KiCAD PCB
    layout. The two are tinted different colors and combined to make a
    more realistic model.
    Note the switch model in KiCAD has a bigger lever than the part
    specified, so it may not look like it aligns correctly.
    [spider_dropper2.scad]
2026-05-27 Added pin bender to main SCAD file and tweaked print layout of parts.
    [spider_dropper2.scad]
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2026-06-03 Improved visualizations by adding motor models and animation.
    The code for the motor models is hacky, but good enough to see what's
    going on. The animation turns the motor shaft, shaft adapter, drive
    gear, hub screw, and spool. The spool even rapidly unwinds for the
    drop.
    [deer_motor_model.scad, jgy_motor_model.scad, spider_dropper2.scad]
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2026-06-04 Added video/demo.py to make illustrative videos.
    This is a crude Python script to generate frames using OpenSCAD's
    command line interface and then to stitch them together with ffmpeg.
    OpenSCAD's own animation generator still doesn't work from the command
    line on Windows, despite somebody accepting my pull request a few
    years ago. So the script generates the frames one at a time.
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2026-06-05 Applied fix to make gears mesh better in preview.
    [spider_dropper2.scad]
2026-06-07 Made incremental progress toward the gears meshing correctly.
    They still re-engage too late, and the drop needs to be parabolic.
    [spider_dropper2.scad]
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2026-06-17 Corrected information about where to put the heat-shrink tubing.
    These are bits that are they to cushion the cable where strain relief
    is applied.
2026-06-21 Revised parts spreadsheet.
    Reflects new parts prices. Credits the Slightly Smarter model for the
    DC barrel pigtail that would have come with the basic DC model. Fixes
    some formatting.
    [spider_dropper_parts.xlsx]
2026-06-21 Deleted the old spider_dropper.scad file. Not going back.
    In a subsequent step, spider_dropper2.scad will will the 2.
    [spider_dropper.scad]
2026-06-21 Renamed spider_dropper2.scad to spider_dropper.scad. NFC.
    The .json file wasn't necessary. Updated the reference in demo.py.
    [spider_dropper.scad]
2026-06-23 Modified the adapter and spline design (again!) for the last time.
    Enables the use of the shaft end screw to keep the adapter from walking
    off the end (which happened in one demo at Norcal Haunters events on
    Saturday). The means old gears won't fit new shaft adapters. Even the
    hub screws had to be tweaked for there to be space for the head of that
    shaft screw.
    [spider_dropper.scad]
